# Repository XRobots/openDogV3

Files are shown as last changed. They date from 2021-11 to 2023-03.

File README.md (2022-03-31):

# openDogV3
CAD and Code for openDog V3: https://www.youtube.com/playlist?list=PLpwJoq86vov8uTgd8_WNgBHFpDYemO-OJ

I've included a Bill of Materials this time, BOM.ods, which is probably complete, I'll be adding to it if I remember anything else.

I used the AS5047 encoders in absolute position mode in this build. Check out the ODrive documentation for more info: https://docs.odriverobotics.com/v/latest/encoders.html You will have to configure the encoder parameters and then run the offset calibration as per the ODrive docmentation. Default offsets are set in the code in the variable declaration section which will need calibrating to move the joints to the default positons in mode 3 below.

ODrive vel_limit and vel_limit_tolerance are set to math.inf within the ODrive tool which stops the motors disarming under certain circumstanses. (You will have to do 'import math' first within the ODrive tool).

Menu options on the Dog/LCD are as follows:

0) nothing / default at power up
1) put motors into closed loop control
2) move legs outwards so they just clear the stand stirrups by 1-2 mm
3) move legs so both shoulder and knee joints are at 45' (the default positions shown in the CAD)
4) turn up motor position, velocity and integrator gains
5) inverse kinematics demo mode for 6 axis of translation and rotation (also makes the legs slightly straighterCancel changes)
6) walking mode (same leg position as 5)
10) put the feet back into position so they rest on the stand stirrups

The remote now has a 'reverse' switch which reverses four axis of the remote so the dog walks backwards. This happens on the remote rather than in the dog's kinematics. There is also a motor enable switch which must be on for the dog to work.

Foot mould CAD is included for silicone rubber feet. I used a 25A Shore hardness Platinum cure silicone with pigment. Note that the Carbon Fibre foot tube is glued into the lower leg and foot insert to stop it rotating.

The parts are all printed in PLA. The larger parts are around 15% infill with 3 perimeters at 0.3mm layer height. The smaller parts such as the Cycloidal drive internals are 4 perimeters and up to 30-40% infill.

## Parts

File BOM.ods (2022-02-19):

Part | desc | quantity | notes | Example item
General Parts
Motor | 9225 90 KV brishless motor | 12 | Either HobbyKing / Turnigy Multistar 9225 90 KV or EaglePower 8308 (stator) 9225 (can) 90 KV motors. | https://www.aliexpress.com/item/4000563826414.html
Belts | HTD 5M pitch 630mm length | 4 | Knee drive belts | https://www.beltingonline.com/htd-pitches-c-40_253/5mm-htd-timing-belts-p-4575.html
Carbon Fiber tube | 28mm OD, 1mm+ wall thickness | 4 | 4 x 1 metre lengths cut to size to match the CAD (cut-offs from the main parts are long enough for the legs) | https://www.ebay.co.uk/itm/333609712747
Electronics
ODrive BLDC motor drivers | ODrive 3.6 | 6 | 2 per axis | https://odriverobotics.com/shop/odrive-v36
Motor encoders | AMS AS5047P motor encoder | 12 | 1 per axis | https://www.digikey.co.uk/en/products/detail/AS5047P-TS_EK_AB/AS5047P-TS_EK_AB-ND/5452344
Microcontroller | Teensy 4.1 | 1 | For Dog | https://coolcomponents.co.uk/products/teensy-4-1-development-board
Microcontroller | Teensy LC | 1 | For Remote | https://coolcomponents.co.uk/products/teensy-lc-with-bootloader
Voltage Regulator | 5V / adjustable regulator | 1 | For Dog electronics - set to 5V to power Teensy etc | https://www.ebay.co.uk/itm/153278406120
IMU | MPU6050 | 1 | For Dog | https://coolcomponents.co.uk/products/mpu-6050-6-dof-accel-and-gyro-sensor-stemma-qt-qwiic
Radio | NRF24L01 | 2 | One in remote and one in Dog | https://www.amazon.co.uk/AZDelivery-NRF24L01-wireless-Arduino-ESP8266/dp/B075DBDS3J
Connectors | 25-Way D-range male | 1 |  | https://www.ebay.co.uk/itm/252433532104
Connectors | 25-Way D-range female | 1 |  | https://www.ebay.co.uk/itm/262493128741
Electronics power switch | latching push switch | 1 |  | https://www.ebay.co.uk/itm/282092882727
E-stop switch | latching push switch | 2 |  | https://www.amazon.co.uk/gp/product/B08927GP2J
Volt Meters | Pan Volt Meters | 2 |  | https://www.amazon.co.uk/gp/product/B07J2NQSFG
LCD | I2C backpack LCD | 1 |  | https://www.amazon.co.uk/Youmile-Interface-Adapter-Arduino-Raspberry-1602-Blue/dp/B08218RPX6
Encoder cable | 6-core foil-sheilded signail cable | 6 | metres, but make sure you have enough | https://www.cef.co.uk/catalogue/products/2592862-6-core-belden-equiv-9536-lsf-shielded-cable-sold-by-the-mtr
Joysticks | 3 axis Joystick | 2 | For remote | https://www.ebay.co.uk/itm/174872424256?epid=18034324627
toggle switches | on/off toggles | 5 | For remote | https://www.ebay.co.uk/itm/133684848765
Push switches | momentary switches | 4 | For remote | https://www.amazon.co.uk/gp/product/B089K8ZTC2
Batteries
Main Battery | 6S High-drain Lipo | 1 | Make sure it can source enough current, mineis 60C. Also requires suitable balance charger | https://hobbyking.com/en_us/zippy-compact-4000mah-6s-60c-lipo-pack.html
Electronics Battery | 2S small battery | 1 | Anything like 2S/3S will do - regulator above is used to get 5V anyway | https://www.amazon.co.uk/URGENEX-Battery-Batteries-1000mah-WLtoys/dp/B08Y8YN283
Breaings
Internal Cycloidal Drive bearings | 12mm OD x 4mm ID x 4mm thickness | 384 | I got these from Aliexpress for $70 for 400. | https://www.aliexpress.com/item/32814388857.html
Cam and cap Drive bearings | 32mm OD x 20mm ID x 7mm thickness | 36 | There are three per drive | https://www.aliexpress.com/item/896891895.html
Top/bottom Drive bearings | 85mm OD x 65mm ID x 10mm thickness | 24 | two per drive | https://www.aliexpress.com/item/4000110681895.html
Thin wall bearings | 37mm OD x 30mm ID x 4mm thickness | 8 | one per leg and two per end bracket. | https://simplybearings.co.uk/shop/p156409/61706ZZ-Budget-Metal-Shielded-Thin-Section-Deep-Groove-Ball-Bearing-30x37x4mm/product_info.html
Knee bearings | 22mm OD x 8mm ID x 7mm thickness | 8 | two per leg for the knee joints | https://simplybearings.co.uk/shop/p170659/608ZZ-Budget-Metal-Shielded-Deep-Groove-Ball-Bearing-8x22x7mm/product_info.html
Knee idler bearings | 19mm OD x 6mm ID, x 6mm thickness | 16 | four per leg for belt idler | https://simplybearings.co.uk/shop/p170642/626ZZ-Budget-Metal-Shielded-Deep-Groove-Ball-Bearing-6x19x6mm/product_info.html
4mm steel bar | 4mm x 31mm length | 132 | one for very bearing mount aroudn the outside of the cycloidal drives | https://www.ebay.co.uk/itm/193950943958
Nuts & Bolts
Motor mounts | M4 12 mm thread length countersunk | 48 | 4 per motor
Cycloidal Drive cam | M4 40mm thread length socket cap | 12 | 1 per drive
Cycloidal Drive cam | M4 Nylon insert locking nuts | 12 | 1 per drive
Cycloidal Drive output | M4 Nylon insert locking nuts | 60 | 5 per drive
Cycloidal Drive output | M4 washers | 60 | 5 per drive
Cycloidal Drive cam | M3 15mm thread length | 48 | 4 per drive
Cycloidal Drive output | M4 hex heads 80mm | 60 | 5 per drive, need cutting to length
Screws
Drive case screws | 2.9mm 18mm length countersunk pozidrive | 132 | 22 per drive, back and front
side-to-side axis mount screws | 2.9mm 18mm length countersunk pozidrive | 48 | 12 per drive for 4 drives
Leg screws | 2.9mm 18mm length countersunk pozidrive | 56 | 18 per leg
Nylon
Washers | 4mm ID Nylon washers | 384 | one top and bottom on each pin, 32 per drive | https://nyfast.com/nylon-washers/10080-26805-standard-flat-nylon-washers
Spacers | 4mm ID Nylon spacers, 5mm length | 192 | 16 per drive | https://nyfast.com/new-products/10497-30283-standard-metric-nylon-spacers

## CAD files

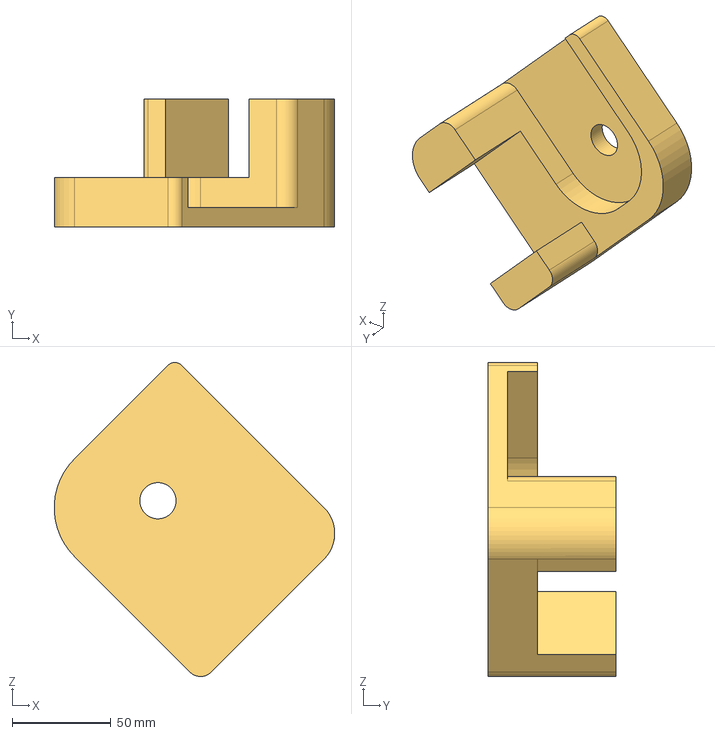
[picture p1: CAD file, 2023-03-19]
CAD/openDogV3_jig_knee.stp
142.3 x 65.0 x 159.4 mm

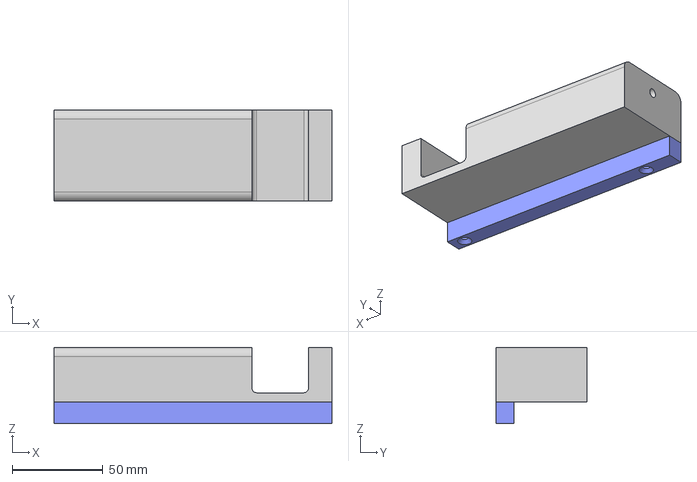
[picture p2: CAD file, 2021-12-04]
CAD/jig.stp
153.0 x 50.0 x 42.0 mm

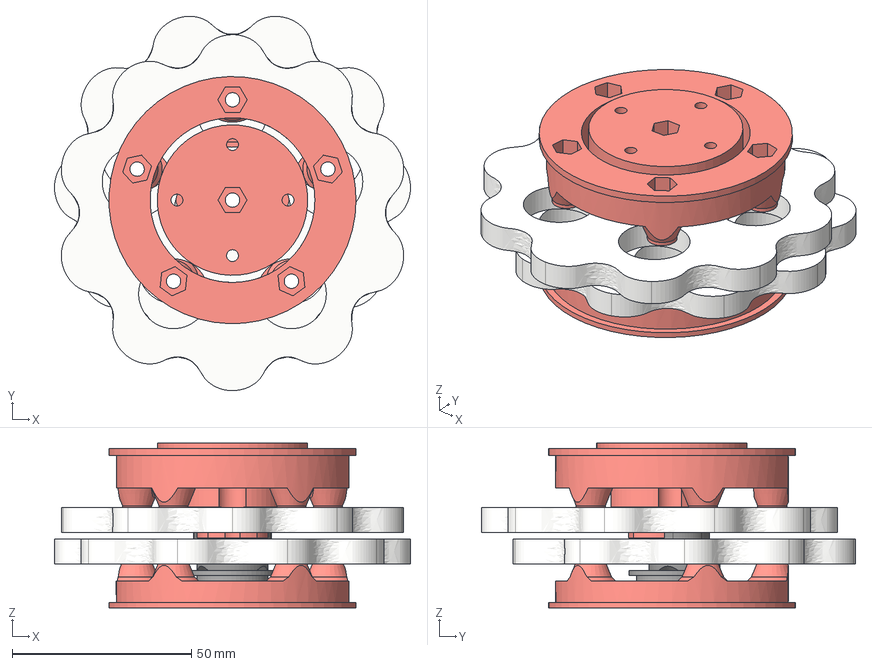
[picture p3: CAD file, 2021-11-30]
CAD/openDog V3_internals_toleranced.stp
99.4 x 104.5 x 46.0 mm

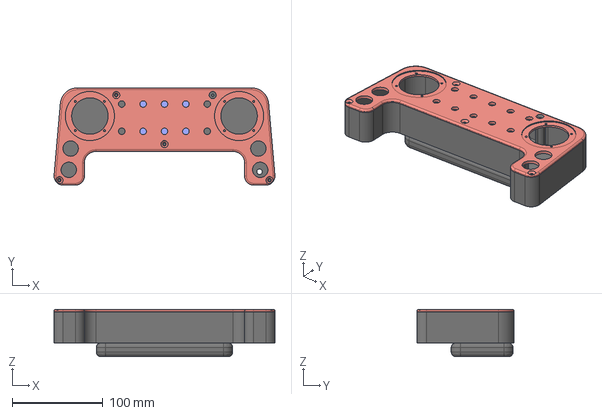
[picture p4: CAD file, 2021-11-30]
CAD/Remote.stp
242.9 x 107.0 x 52.0 mm

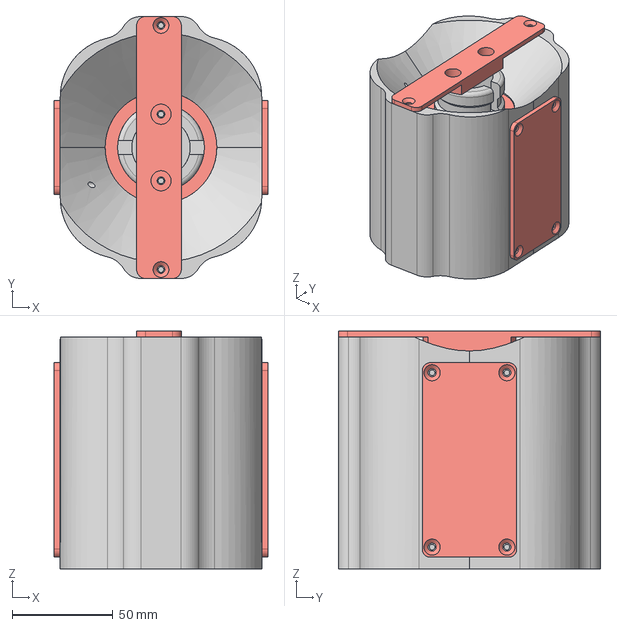
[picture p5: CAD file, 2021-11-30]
CAD/openDog V3_foot.stp
106.0 x 130.0 x 118.0 mm

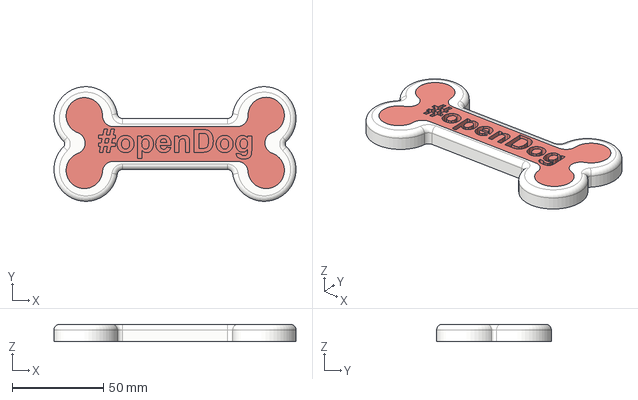
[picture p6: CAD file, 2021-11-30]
CAD/bone.stp
132.9 x 63.0 x 9.50 mm

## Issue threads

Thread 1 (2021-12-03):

BOM Edit - Steel Rod

twodawg, 2021-12-03:
Can you let us know how long (and how many) and the diameter size (4 mm?) you used as a steel rod to hold the bearings in each motor housing? I did not see it in the BOM.

I am super excited to upgrade my V2 Opendog to V3!

XRobots, 2021-12-04:
Thanks, I updated the BOM and also uploaded the jig I used to cut them. 31mm long, 4mm diameter.

ghent360, 2022-01-05:
Btw one can order 30mm long 4mm dowel pins. It would be great if those can be used. Alternatively the next standard size is 35mm.

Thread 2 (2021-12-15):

Account for Foot in Kinematics

Yay295, 2021-12-15:
Based on this diagram from your [kinematics video](https://www.youtube.com/watch?v=eKZIJwJBjEs), the end point of the leg is currently at the tip of the foot. However, as you stated in the video, the tip of the foot is not necessarily the point touching the ground. To account for this the end point of the leg should actually be at the center of the foot when doing the calculations. The point touching the ground would then be one foot's radius from this point.

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

XRobots, 2021-12-15:
Yes the legs are too short - in V2 I used the middle of the ball, so the CF tubes should just be a bit longer.  The centre positions will change as the foot rolls over though so there's still some error. Either way the whole thing is compliant so it's negligible.

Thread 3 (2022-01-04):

Encoders in BOM

ghent360, 2022-01-04:
Hi, are the encoders listed in the bom the ones you use in the video. By looking at the link the specified ones are just AMS magnetic encoder on a PCB with a magnet. The ones I see in your videos look quite different with a whole housing.

ghent360, 2022-01-04:
Also the magnetic encoders would need a magnet of some sort to be attached to the axis, do these come with the motor board?

XRobots, 2022-01-04:
I updated the BOM with links, it's this one, and it ships with the magnet: https://www.digikey.co.uk/en/products/detail/AS5047P-TS_EK_AB/AS5047P-TS_EK_AB-ND/5452344

ghent360, 2022-01-05:
Thank you. I saw you use the boards in one of your other videos.

Closed 2022-01-05.

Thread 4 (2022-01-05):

STL files and print instructions

ghent360, 2022-01-05:
Thank you for publishing the CAD files as open source.

Would it be possible to extract the STL files for the 3d printer parts and provide some guidance as how to best print those parts?
For example the part orientation, print settings like (number of perimeter walls, infill percentage, support material?)

For parts that need to be printed multiple times, I would recommend adding a suffix _xN (where N is the number of times the part needs to be printed). Also if you want to provide some guidance to the part color you can name parts should be printed in "alternate" color with a_ prefix.

(I would not take credit for this naming scheme, it is used by the Voron printer project and it works well there)

danielwdunn, 2022-06-08:
Hello, I'm looking for the same information/guidance. Did you happen to print this already or export the STLs from the step files?

XRobots, 2022-06-08:
It's designed to all be printed in PLA, but you could use tougher materials and skinny some of it down. I used 4 perimeters for everything at 0.3mm layer height with a 0.5mm nozzle. Infill was down to 10-15% for the big parts and 20-30% for the small parts like the cycloidal discs/small motor components etc.

ghent360, 2022-06-09:
First I want to say thank you to James for sharing this excellent project. It seems a lot of though went into it and I really appreciate the chance to be able to replicate your work.

I agree exporting the STLs seems like a tedious task. The trick is not to 3d print the models of the bearings, but one learns.

@XRobots for the internals of the transmission parts should one use the file called 'openDog V3_internals_toleranced' ?

danielwdunn, 2022-06-09:
Truly an incredible and impressive OpenSource project. I'm hoping to put together a full build guide for openDog v3 (if one doesn't exist yet). And I will include the information provided here and any I learn along the way.

XRobots, 2022-06-09:
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

That is another set of parts I toleranced for my printer.

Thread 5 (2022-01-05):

Add battery types to the BOM

ghent360, 2022-01-05:
I guess from your video the main battery is some 6S lipo type.

Can you also add the electronics and remote battery types?

XRobots, 2022-01-05:
I'll add the batteries to the BOM. Yes the main battery is 6S but it's quite high drain, so I have 60C battery(s).

The smaller one powering the electronics is 7.4v - I'll find a link for it, but anything over 6v will do.

Closed 2022-01-07.

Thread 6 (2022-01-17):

Please add the idler bearing to BOM

ghent360, 2022-01-17:
Your test leg video mentions 6mm ID bearings for the idlers, that are not in the BOM. Please add.

XRobots, 2022-01-17:
done, thanks

Closed 2022-01-17.

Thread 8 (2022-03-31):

Broken link

3laws, 2022-03-31:
Link [https://docs.odriverobotics.com/encoders](https://docs.odriverobotics.com/encoders)  is 404

XRobots, 2022-03-31:
ODrive updated their documentation - I've edited the link

Closed 2022-03-31.

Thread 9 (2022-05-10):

STP file disassembly is not working

MateKristof, 2022-05-10:
Could You tell me what is the CAD software do You use? When I open the STP file in Solid Edge or Inventor then the assembled parts in the assembly appears as only one big standart parts. I am not able to disassemble them. As You see in the shoulder connections:

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

**I would highly appreciate if You were kind and upload the native CAD software files**, like SolidWorks .sldprt / .sldasm or Solid Edge .par / .asm and so on.

XRobots, 2022-05-11:
It was done in Fision360, but it's a STEP file so it's just a bunch of solid objects. I know there are several people who are building it...  I've never used Inventor I'm afraid.

ghent360, 2022-06-09:
Some CAD software does have issues with the STEP file from fusion. I did use some STEP file analyzer (https://www.nist.gov/services-resources/software/step-file-analyzer-and-viewer) and it found no issues with the STEP file per se, so it has to be something in the import that chokes.

What I found works best is if you import the step file back in fusion 360 and then you can re-export only parts and that works a bit better.

Best of luck.

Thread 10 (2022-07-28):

Assemblies for Different CAD Programs

DrYogurt, 2022-07-28:
I'm having some difficulties importing the step files as assemblies (In FreeCAD SolidWorks and Fusion) parts load in as bodies and no import settings seem able to fix it. This is probably due to my inexperience with importing stps, but I would appreciate a zip of a Fusion or SolidWorks assembly.

Thanks

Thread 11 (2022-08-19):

ODrive 3.6 Voltage?

danielwdunn, 2022-08-19:
What voltage should be selected when ordering the ODrive 3.6?

Are there alternatives to this item? It's currently the most expensive piece of the entire project. Total cost is about $1500 USD for the six pieces of ODrive 3.6. Though, I did find another supplier on Aliexpress that may reduce the price to around $1000 or so.

XRobots, 2022-08-19:
I bought the 56V version because a 6S lipo will charge up to 25V+

I've not tried any alternatives. I haven't tried the ones on Aliexpress but they are likely to be clones of random hardware versions so the latest firmware may not work correctly.

danielwdunn, 2022-08-19:
Thank you! I ordered the Aliexpress 56v version and will test it. I'm working on an updated BOM for folks in the US/North America. I'll share it once complete.

dylanireland, 2022-11-02:
@danielwdunn Have you happened to receive and/or test the Aliexpress clone of the ODrive? Very interested to see your BOM when complete!

XRobots, 2022-11-03:
I've not tried them, but a lot of them look like the pins aren't in the same place, so they are clones of previous versions of hardware which means the pin mappings will be wrong and not everything will work as expexted.

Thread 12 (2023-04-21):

BOM: 5mm HTD® Timing Belts Width ?

bryn51, 2023-04-21:
Please specify the width of the timing belts needed.  Choices (standard) are 9 mm, 15 mm and 25 mm.  I'm guessing it might be 15 mm

ronzelver, 2023-04-21:
> Please specify the width of the timing belts needed.  Choices (standard) are 9 mm, 15 mm and 25 mm.  I'm guessing it might be 15 mm

15mm might just fit, but the ones I've used are 9mm wide and I think those are the ones originally referenced by James as well.

bryn51, 2023-04-21:
All good, thanks.

If not obvious, I am trying to cost out the project using the BOM.

Cheers

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

bryn51, 2023-04-24:
Thanks for your response.

Just by the by... looks like just buying the stuff needed is nightmareish. I discovered the chinese manufacturers of CF tubing do not even have testing facilities for their tubing, cant tell me how stiff is the tubing or what the breaking point(s) are.  Maybe I should be less persnickety.

f-e-l-i-x, 2023-05-31:
@ronzelver I saw your finished openDog on youtube, looks great! How much would I have to spend on building one of them?

ronzelver, 2023-05-31:
> @ronzelver I saw your finished openDog on youtube, looks great! How much would I have to spend on building one of them?

Total cost is around 2500~3000 EUR. The drives, controllers and bearings alone were already 1850 EUR.

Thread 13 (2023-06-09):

Suggestion: Checkout Dingo open source robot dog

lucasfolino, 2023-06-09:
Found this and thought you could use some of the techniques to further improve openDog.  Especially the linkage for the legs.  It seems to have better stability, control, and range of motion.  Also seems to have better response.  The Dingo isn't as long or string, but I think that these techniques could vastly improve the operation of open dog.  Also seems like they solved other issues as well.

https://www.youtube.com/watch?v=8KntOIgzUjY
https://github.com/Yerbert/DingoQuadruped
https://grabcad.com/library/dingo-robot-quadruped-2

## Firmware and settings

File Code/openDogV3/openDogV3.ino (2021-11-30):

//ODrive
#include <ODriveArduino.h>

// Radio
#include <SPI.h>
#include <nRF24L01.h>
#include <RF24.h>

//I2C LCD
#include <LiquidCrystal_I2C.h>
LiquidCrystal_I2C lcd(0x27, 16, 2); // set the LCD address to 0x27 for a 16 chars and 2 line display

// ramp lib
#include <Ramp.h>

RF24 radio(9, 10); // CE, CSN
const byte addresses[][6] = {"00001", "00002"};

// Printing with stream operator
template<class T> inline Print& operator <<(Print &obj,     T arg) {
  obj.print(arg);
  return obj;
}
template<>        inline Print& operator <<(Print &obj, float arg) {
  obj.print(arg, 4);
  return obj;
}


//ODrive Objects
ODriveArduino odrive1(Serial1);
ODriveArduino odrive2(Serial2);
ODriveArduino odrive3(Serial3);
ODriveArduino odrive4(Serial4);
ODriveArduino odrive5(Serial5);
ODriveArduino odrive6(Serial6);

//**************remote control****************
struct RECEIVE_DATA_STRUCTURE {
  //put your variable definitions here for the data you want to send
  //THIS MUST BE EXACTLY THE SAME ON THE OTHER ARDUINO
  int16_t menuDown;
  int16_t Select;
  int16_t menuUp;
  int16_t toggleBottom;
  int16_t toggleTop;
  int16_t toggle1;
  int16_t toggle2;
  int16_t mode;
  int16_t RLR;
  int16_t RFB;
  int16_t RT;
  int16_t LLR;
  int16_t LFB;
  int16_t LT;
};

RECEIVE_DATA_STRUCTURE mydata_remote;

int toggleTopOld;
int remoteState;
int remoteStateOld;

float RLR = 0;
float RFB = 0;
float RT = 340;
float LLR = 0;
float LFB = 0;
float LT = 0;

float RLRFiltered = 0;
float RFBFiltered = 0;
float RTFiltered = 340;
float LLRFiltered = 0;
float LFBFiltered = 0;
float LTFiltered = 0;
int filterFlag1 = 0;

unsigned long currentMillis;
long previousMillis = 0;    // set up timers
long interval = 10;        // time constant for timer
unsigned long count;

long previousInterpMillis = 0;    // set up timers
int interpFlag = 0;

unsigned long remoteMillis;

int stepFlag = 0;
long previousStepMillis = 0;
int stepStartFlag = 0;

int requested_state;
int mode;
int modeOld;
int modeFlag;
int menuFlag;
int modeConfirm;
int modeConfirmFlag = 0;
int runMode = 0;

float longLeg1;
float shortLeg1;
float legLength1;
float longLeg2;
float shortLeg2;
float legLength2;
float footOffset;

float fr_RFB;
float fl_RFB;
float bl_RFB;
float br_RFB;
float fr_RLR;
float fl_RLR;
float bl_RLR;
float br_RLR;;
float fr_LT;
float fl_LT;
float bl_LT;
float br_LT;

float fr_LLR;
float fl_LLR;
float br_LLR;
float bl_LLR;

float actPos1;
float actPos2;
float actPos3;
float actPos4;

int timer1;   // FB gait timer
int timer2;   // LR gait timer
int timer3;   // Yaw gait timer
float timerScale;   // resulting timer after calcs
float timerScale2;   // multiplier

// ODrive offsets from power up
// ratio is 10:1 so 1 'turn' is 36'.


float offSet20 = -0.3;      //ODrive 2, axis 0     // knee - right front
float offSet30 = 0.6;      //ODrive 3, axis 0     // knee - right rear
float offSet50 = 0.15;      //ODrive 5, axis 0     // knee - left front
float offSet60 = 0.05;      //ODrive 6, axis 0     // knee - left rear

float offSet21 = 0;      //ODrive 2, axis 1     // shoulder - right front
float offSet31 = 0.35;      //ODrive 3, axis 1     // shoulder - right rear
float offSet51 = 0.55;      //ODrive 5, axis 0     // shoulder - left front
float offSet61 =  0.05;      //ODrive 6, axis 1     // shoulder - left rear

float offSet10 = 0.27;      //ODrive 1, axis 0     // hips - right front
float offSet11 = 0.1;      //ODrive 1, axis 1     // hips - right back
float offSet40 = 0.07;      //ODrive 4, axis 0     // hips - left front
float offSet41 = 0.35;      //ODrive 4, axis 1     // hips - left back


// ** test varibles

      int tester;
      int tester2;
      //long previousStepMillis = 0;    // set up timers
      //int stepFlag = 0;
      float z;
      float x;


//***********************************
//***********************************
class Interpolation {
  public:
    rampInt myRamp;
    int interpolationFlag = 0;
    int savedValue;

    int go(int input, int duration) {

      if (input != savedValue) {   // check for new data
        interpolationFlag = 0;
      }
      savedValue = input;          // bookmark the old value

      if (interpolationFlag == 0) {                                        // only do it once until the flag is reset
        myRamp.go(input, duration, LINEAR, ONCEFORWARD);              // start interpolation (value to go to, duration)
        interpolationFlag = 1;
      }

      int output = myRamp.update();
      return output;
    }
};    // end of class

Interpolation interpFRX;        // interpolation objects
Interpolation interpFRY;
Interpolation interpFRZ;
Interpolation interpFRT;

Interpolation interpFLX;        // interpolation objects
Interpolation interpFLY;
Interpolation interpFLZ;
Interpolation interpFLT;

Interpolation interpBRX;        // interpolation objects
Interpolation interpBRY;
Interpolation interpBRZ;
Interpolation interpBRT;

Interpolation interpBLX;        // interpolation objects
Interpolation interpBLY;
Interpolation interpBLZ;
Interpolation interpBLT;

//***********************************
//***********************************

// ****************** SETUP ******************************

void setup() {


  // initialize serial communication
  Serial.begin(115200);

  Serial1.begin(115200);
  Serial2.begin(115200);
  Serial3.begin(115200);
  Serial4.begin(115200);
  Serial5.begin(115200);
  Serial6.begin(115200);


  radio.begin();
  radio.openWritingPipe(addresses[0]); // 00002
  radio.openReadingPipe(1, addresses[1]); // 00001
  radio.setPALevel(RF24_PA_MIN);

  radio.startListening();

  //LCD
  lcd.init();
  lcd.backlight();
  lcd.setCursor(0, 0);
  lcd.print("openDog V3");
  lcd.setCursor(0, 1);
  lcd.print("S:0  C:0");

}   // end of setup

// ********************* MAIN LOOP *******************************

void loop() {

  currentMillis = millis();
  if (currentMillis - previousMillis >= 10) {  // start timed event

    previousMillis = currentMillis;


    // check for radio data
    if (radio.available()) {
      radio.read(&mydata_remote, sizeof(RECEIVE_DATA_STRUCTURE));
      remoteMillis = currentMillis;
    }

    // is the remote disconnected for too long ?
    if (currentMillis - remoteMillis > 500) {
      remoteState = 0;
    }
    else {
      remoteState = 1;
    }    

    // threshold remote data
    // some are reversed based on stick wiring in remote
    RFB = (thresholdStick(mydata_remote.RFB)) * -1;
    RLR = (thresholdStick(mydata_remote.RLR));
    RT = thresholdStick(mydata_remote.RT);
    LFB = (thresholdStick(mydata_remote.LFB)) * -1;
    LLR = thresholdStick(mydata_remote.LLR);
    LT = thresholdStick(mydata_remote.LT);

    
    // stop the dog if the remote becomes disconnected
    if (remoteState == 0) {     
      RFB = 0;
      RLR = 0;
      RT = 0;
      LFB = 0;
      LLR = 0;
      LT = 0;
    }


    // mode select

    if (mydata_remote.menuUp == 1 && menuFlag == 0) {
      menuFlag = 1;
      mode = mode + 1;
      mode = constrain(mode, 0, 10);
    }
    else if (mydata_remote.menuDown == 1 && menuFlag == 0) {
      menuFlag = 1;
      mode = mode - 1;
      mode = constrain(mode, 0, 10);
    }
    else if (mydata_remote.menuDown == 0 && mydata_remote.menuUp == 0) {
      menuFlag = 0;
    }

    if (mode != modeOld) {            // only update the LCD if the data has changed
      lcd.setCursor(0, 1);
      lcd.print("    ");
      lcd.setCursor(0, 1);
      lcd.print("S:");
      lcd.print(mode);
    }
    modeOld = mode;       // bookmark previous data so we can see if it's changed

    if (mydata_remote.Select == 1) {
      modeConfirm = mode;             // make the actual mode be the potential mode when the select button is pressed
      lcd.setCursor(5, 1);            // display current mode on LCD
      lcd.print("    ");
      lcd.setCursor(5, 1);
      lcd.print("C:");
      lcd.print(modeConfirm);
    }

    // display remote connection state
    if (remoteState != remoteStateOld) {
      if (remoteState == 0) {
        lcd.setCursor(13, 0);
        lcd.print("N");
      }
      else if (remoteState == 1) {
        lcd.setCursor(13, 0);
        lcd.print("C");
      }
    }
    remoteStateOld = remoteState;

    // display motor enable state

    if (mydata_remote.toggleTop != toggleTopOld) {
      if (mydata_remote.toggleTop == 1) {
        lcd.setCursor(15, 0);
        lcd.print("E");
      }
      else if (mydata_remote.toggleTop == 0) {
        lcd.setCursor(15, 0);
        lcd.print("D");
      }
    }
    toggleTopOld = mydata_remote.toggleTop;

    // ****** MAIN MENU ******* 

    if (mydata_remote.Select == 0) {                            // make sure the button is released before it can be pressed again
              modeConfirmFlag = 0;
    }

    if (modeConfirm == 1 && modeConfirmFlag == 0 && mydata_remote.Select == 1) {             // init ODrives with low gains
      Serial.println("Init Odrives mode 1");
      OdriveInit1();
      modeConfirmFlag = 1;
    }

    else if (modeConfirm == 2 && modeConfirmFlag == 0 && mydata_remote.Select == 1) {       // default to 45' shoulder and knees
      Serial.println("Knees mode 2");
      applyOffsets1();
      modeConfirmFlag = 1;
    }

    else if (modeConfirm == 3 && modeConfirmFlag == 0 && mydata_remote.Select == 1) {       // default to hip position
      Serial.println("Shoulders mode 3");
      applyOffsets2();
      modeConfirmFlag = 1;
    }

    else if (modeConfirm == 4 && modeConfirmFlag == 0 && mydata_remote.Select == 1) {       // turn up gains
      Serial.println("Modify Gains mode 4");
      modifyGains();
      modeConfirmFlag = 1;
    }

    else if (modeConfirm == 5 && modeConfirmFlag == 0 && mydata_remote.Select == 1) {       // turn up gains
      Serial.println("Kinematics mode 5");
      interpFlag = 0;
      previousInterpMillis = currentMillis;
      runMode = 1;
      modeConfirmFlag = 1;
    }

    else if (modeConfirm == 6 && modeConfirmFlag == 0 && mydata_remote.Select == 1) {       // turn up gains
      Serial.println("Walking Mode 6");
      interpFlag = 0;
      previousInterpMillis = currentMillis;
      runMode = 2;
      modeConfirmFlag = 1;
    }

    else if (modeConfirm == 10 && modeConfirmFlag == 0 && mydata_remote.Select == 1) {       // turn up gains
      Serial.println("Going Home Mode 10");
      interpFlag = 0;
      previousInterpMillis = currentMillis;
      runMode = 10;
      modeConfirmFlag = 1;
    }

    else if (modeConfirm == 9 && modeConfirmFlag == 0 && mydata_remote.Select == 1) {       // turn up gains
      Serial.println("Interp Test");
      interpFlag = 0;
      previousInterpMillis = currentMillis;
      runMode = 9;
      modeConfirmFlag = 1;
    }
    
    // **** END OF MAIN MENU **** 

    if (runMode == 9) {     // iterpolation testing

      if (stepFlag == 0 && currentMillis - previousStepMillis > 1000) {
          tester = 0;
          tester2 = 300.5;
          stepFlag = 1;
          previousStepMillis = currentMillis;
          }

      else if (stepFlag == 1 && currentMillis - previousStepMillis > 1000) {
          tester = 100.6;
          tester2 = 0;
          stepFlag = 0;
          previousStepMillis = currentMillis;
          }

        z = interpFRZ.go(tester,500);
        x = interpFRY.go(tester2,500);
            
        Serial.print(stepFlag);
        Serial.print(" , ");
        Serial.print(tester);
        Serial.print(" , ");
        Serial.print(z);
        Serial.print(" , ");
        Serial.println(x);      
    }

    if (runMode == 10) {         // put the legs back on the stand

        int offset1 = 70;

        kinematics (1, -offset1, 0, 300, 0, 0, 0, 0, 0);   // front right
        kinematics (2, -offset1, 0, 300, 0, 0, 0, 0, 0);   // front left
        kinematics (3, offset1, 0, 300, 0, 0, 0, 0, 0);   // back left
        kinematics (4, offset1, 0, 300, 0, 0, 0, 0, 0);   // back right
    }

    else if (runMode == 1) {
      
    // ** inverse kinematics demo ** 

        // scale sticks to mm
        RFB = map(RFB,-462,462,-100,100);
        RLR = map(RLR,-462,462,-100,100);        
        RT = map(RT,-462,462,240,440);
        RT = constrain(RT,240,380);      
        LFB = map(LFB,-462,462,-15,15);        
        LLR = map(LLR,-462,462,-15,15);        
        LT = map(LT,-462,462,-20,20);      

        // filter sticks
        RFBFiltered = filter(RFB, RFBFiltered, 40);
        RLRFiltered = filter(RLR, RLRFiltered, 40);
        RTFiltered = filter(RT, RTFiltered, 40);
        LFBFiltered = filter(LFB, LFBFiltered, 40);
        LLRFiltered = filter(LLR, LLRFiltered, 40);
        LTFiltered = filter(LT, LTFiltered, 40);
                  
        kinematics (1, RFBFiltered, RLRFiltered, RTFiltered, LLRFiltered, LFBFiltered, LTFiltered, 0, 0);   // front right
        kinematics (2, RFBFiltered, RLRFiltered, RTFiltered, LLRFiltered, LFBFiltered, LTFiltered, 0, 0);   // front left
        kinematics (3, RFBFiltered, RLRFiltered, RTFiltered, LLRFiltered, LFBFiltered, LTFiltered, 0, 0);   // back left
        kinematics (4, RFBFiltered, RLRFiltered, RTFiltered, LLRFiltered, LFBFiltered, LTFiltered, 0, 0);   // back right
      
 }

   else if (runMode == 2) {
      // simple walking
      
      RFB = map(RFB,-462,462,-50,50);  // mm
      RLR = map(RLR,-462,462,-25,25);  // mm
      LT = map(LT,-462,462,-25,25);      // degrees 

      RFBFiltered = filter(RFB, RFBFiltered, 15);
      RLRFiltered = filter(RLR, RLRFiltered, 15);
      LTFiltered = filter(LT, LTFiltered, 15);

      longLeg1 = 340;
      shortLeg1 = 250;
      longLeg2 = 340;
      shortLeg2 = 250;

      footOffset = 0;
      timer1 = 75;   // FB gait timer
      //timer2 = 75;   // LR gait timer
      //timer3 = 75;   // LR gait timer

      if (RFBFiltered > -0.1 && RFBFiltered < 0.1 && RLRFiltered > -0.1 && RLRFiltered < 0.1  && LTFiltered > -0.1 && LTFiltered < 0.1 ) {    // controls are centred or near enough

      
      // position legs a default standing positionS
          legLength1 = longLeg1;
          legLength2 = longLeg2;
          fr_RFB = 0;
          fl_RFB = 0;
          bl_RFB = 0;
          br_RFB = 0;
          fr_RLR = footOffset;
          fl_RLR = -footOffset;
          bl_RLR = -footOffset;
          br_RLR = footOffset;
          fr_LT = 0;
          fl_LT = 0;
          bl_LT = 0;
          br_LT = 0;        
      }
      
      //walking
      else {


          //Serial.println(timerScale);
        
          if (stepFlag == 0 && currentMillis - previousStepMillis > timerScale) {
              legLength1  = shortLeg1;
              legLength2 = longLeg2; 
              fr_RFB = 0-RFBFiltered;
              fl_RFB = RFBFiltered;
              bl_RFB = 0-RFBFiltered;
              br_RFB = RFBFiltered;
              fr_RLR = (footOffset -RLRFiltered) + LT;
              fl_RLR = (-footOffset +RLRFiltered) - LT;
              bl_RLR = (-footOffset - RLRFiltered) - LT;
              br_RLR = (footOffset + RLRFiltered) + LT;
              //fr_RLR = LT;
              //fl_RLR = 0-LT;
              //bl_RLR = 0-LT;
              //br_RLR = LT;
              stepFlag = 1;              
              previousStepMillis = currentMillis;
          }

          else if (stepFlag == 1 && currentMillis - previousStepMillis > timerScale) {
              legLength1 = longLeg1;
              legLength2 = longLeg2;
              fr_RFB = 0-RFBFiltered;
              fl_RFB = RFBFiltered;
              bl_RFB = 0-RFBFiltered;
              br_RFB = RFBFiltered;
              fr_RLR = (footOffset -RLRFiltered) + LT;
              fl_RLR = (-footOffset +RLRFiltered) - LT;
              bl_RLR = (-footOffset -RLRFiltered) - LT;
              br_RLR = (footOffset +RLRFiltered) + LT;
              //fr_RLR = LT;
              //fl_RLR = 0-LT;
              //bl_RLR = 0-LT;
              //br_RLR = LT;                        

              stepFlag = 2;              
              previousStepMillis = currentMillis;
          }

          else if (stepFlag == 2 && currentMillis - previousStepMillis > timerScale) {
              legLength1 = longLeg1;
              legLength2 = shortLeg2;
              fr_RFB = RFBFiltered;
              fl_RFB = 0-RFBFiltered;
              bl_RFB = RFBFiltered;
              br_RFB = 0-RFBFiltered;
              fr_RLR = (footOffset +RLRFiltered) - LT;
              fl_RLR = (-footOffset -RLRFiltered) + LT;
              bl_RLR = (-footOffset +RLRFiltered) + LT;
              br_RLR = (footOffset -RLRFiltered) - LT;
              //fr_RLR = 0-LT;
              //fl_RLR = LT;
              //bl_RLR = LT;
              // br_RLR = 0-LT; 
              stepFlag = 3;              
              previousStepMillis = currentMillis;
          }

          else if (stepFlag == 3 && currentMillis - previousStepMillis > timerScale) {
              legLength1 = longLeg1;
              legLength2 = longLeg2;
              fr_RFB = RFBFiltered;
              fl_RFB = 0-RFBFiltered;
              bl_RFB = RFBFiltered;
              br_RFB = 0-RFBFiltered;
              fr_RLR = (footOffset +RLRFiltered) - LT;
              fl_RLR = (-footOffset -RLRFiltered) + LT;
              bl_RLR = (-footOffset +RLRFiltered) + LT;
              br_RLR = (footOffset -RLRFiltered) - LT;
              //fr_RLR = 0-LT;
              //fl_RLR = LT;
              //bl_RLR = LT;
              //br_RLR = 0-LT; 
              stepFlag = 0;              
              previousStepMillis = currentMillis;
          }

           
          float stepLength;
          float stepWidth;
          float stepAngle;
          float stepHyp;

          // timer calcs

          stepLength = abs(fr_RFB);
          stepWidth = abs(fr_RLR);

          if (stepLength == 0.0) {
            stepLength = 0.01;   // avoid divide by zero
          }

          stepAngle = atan(stepLength/stepWidth);  // radians       // work out actual distance of step
          stepHyp = abs(stepLength/sin(stepAngle));    // mm

          timerScale =  timer1 + (stepHyp/3.5);         
          
      }
   
      kinematics (1, fr_RFB, fr_RLR, legLength1, 0, 0, 0, 1, (timerScale*0.8));   // front right
      kinematics (2, fl_RFB, fl_RLR, legLength2, 0, 0, 0, 1, (timerScale*0.8));   // front left
      kinematics (3, bl_RFB, bl_RLR, legLength1, 0, 0, 0, 1, (timerScale*0.8));   // back left
      kinematics (4, br_RFB, br_RLR, legLength2, 0, 0, 0, 1, (timerScale*0.8));   // back right             
   }



  }     // end of timed loop

}       // end  of main loop

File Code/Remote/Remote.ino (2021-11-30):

#include <SPI.h>
#include <nRF24L01.h>
#include <RF24.h>

#include <Wire.h>  // Comes with Arduino IDE
#include <LiquidCrystal_I2C.h>

// Set the pins on the I2C chip used for LCD connections (Some LCD use Address 0x27 and others use 0x3F):
LiquidCrystal_I2C lcd(0x27,20,4);  // set the LCD address to 0x27 for a 16 chars and 2 line display

unsigned long previousMillis = 0;
const long interval = 20;

int but1;
int but2;
int but3;
int but4;

int sw1;
int sw2;
int sw3;
int sw4;
int sw5;

int axis1;
int axis2;
int axis3;
int axis4;
int axis5;
int axis6;

String count;

struct SEND_DATA_STRUCTURE{
//struct __attribute__((__packed__)) SEND_DATA_STRUCTURE{
  //put your variable definitions here for the data you want to send
  //THIS MUST BE EXACTLY THE SAME ON THE OTHER ARDUINO

    int16_t menuDown;  
    int16_t Select;    
    int16_t menuUp;  
    int16_t toggleBottom;  
    int16_t toggleTop; 
    int16_t toggle1;
    int16_t toggle2;
    int16_t mode;  
    int16_t RLR;
    int16_t RFB;
    int16_t RT;
    int16_t LLR;
    int16_t LFB;
    int16_t LT;

};

struct RECEIVE_DATA_STRUCTURE_REMOTE{
  //put your variable definitions here for the data you want to receive
  //THIS MUST BE EXACTLY THE SAME ON THE OTHER ARDUINO
  int16_t mode;
  int16_t count;
};

int remoteFlag = 0;

SEND_DATA_STRUCTURE mydata_send;
RECEIVE_DATA_STRUCTURE_REMOTE mydata_remote;

RF24 radio(14, 10); // CE, CSN
const byte addresses[][6] = {"00001", "00002"};


void setup() {  

  lcd.init();  // initialize the lcd 
  lcd.backlight();

  pinMode(0, INPUT_PULLUP);
  pinMode(1, INPUT_PULLUP);
  pinMode(2, INPUT_PULLUP);
  pinMode(3, INPUT_PULLUP);
  pinMode(4, INPUT_PULLUP);  
  pinMode(5, INPUT_PULLUP); 
  pinMode(6, INPUT_PULLUP); 
  pinMode(7, INPUT_PULLUP);
  pinMode(8, INPUT_PULLUP);
  
  pinMode(A1, INPUT);
  pinMode(A2, INPUT);
  pinMode(A4, INPUT);
  pinMode(A5, INPUT);
  pinMode(A6, INPUT);
  pinMode(A7, INPUT);
  
  radio.begin();
  radio.openWritingPipe(addresses[1]); // 00001
  radio.openReadingPipe(1, addresses[0]); // 00002
  radio.setPALevel(RF24_PA_MIN);

  radio.stopListening();

  lcd.begin(20,4);   // Initialize the lcd for 20 chars 4 lines, turn on backlight

  lcd.setCursor(0,0);
  lcd.print("Everything Remote   ");
  lcd.setCursor(0,1);
  lcd.print("XRobots.co.uk       ");

  Serial.begin(115200);
 
    
}

void loop() {

     unsigned long currentMillis = millis();
         if (remoteFlag == 0 && currentMillis - previousMillis >= 10) { 

              previousMillis = currentMillis;  

              but1 =  digitalRead(2);
              but2 =  digitalRead(3);
              but3 =  digitalRead(0);
              but4 =  digitalRead(1);

              sw1 = digitalRead(4);
              sw2 = digitalRead(5);
              sw3 = digitalRead(6);
              sw4 = digitalRead(8);
              sw5 = digitalRead(7);

                           
              if (but1 == 0) {
                mydata_send.menuDown = 1;
              }
              else {
                mydata_send.menuDown = 0;
              }

              if (but4 == 0) {
                mydata_send.Select = 1;
              }
              else {
                mydata_send.Select = 0;
              }
                            
              if (but2 == 0) {
                mydata_send.menuUp = 1;
              }
              else {
                mydata_send.menuUp = 0;
              }

              
              
              if (sw2 == 0) {
                mydata_send.toggleBottom = 1;
              }
              else {
                mydata_send.toggleBottom = 0;
              }
              
              if (sw1 == 0) {
                mydata_send.toggleTop = 1;
              }
              else {
                mydata_send.toggleTop = 0;
              }

              //******************

              if (sw3 == 0) {
                mydata_send.toggle1 = 1;
              }
              else {
                mydata_send.toggle1 = 0;
              }
              
              if (but3 == 0) {
                mydata_send.toggle2 = 1;
              }
              else {
                mydata_send.toggle2 = 0;
              } 
                       
              axis1 = analogRead(A5);
              axis2 = analogRead(A4);
              axis3 = analogRead(A6);
              axis4 = analogRead(A3);
              axis5 = analogRead(A2);
              axis6 = analogRead(A1);            

              axis2 = map(axis2,0,1023,1023,0);   // reverse some axis due to physical wiring
              axis4 = map(axis4,0,1023,1023,0);   // reverse some axis due to physical wiring

              // reverse walking & reverse all controls (twist is unaffected because CW and CCW and still the same no matter which way around it is)
              
              if (sw5 == 0) {
                axis1 = map(axis1,0,1023,1023,0);   // reverse axis
                axis2 = map(axis2,0,1023,1023,0);   // reverse axis
                axis4 = map(axis4,0,1023,1023,0);   // reverse axis
                axis5 = map(axis5,0,1023,1023,0);   // reverse axis
              }
              
              axis6 = map(axis6,0,1023,1023,0);   // reverse some axis due to physical wiring            
             
              mydata_send.RFB = axis1;
              mydata_send.RLR = axis2;
              mydata_send.RT = axis3;
              mydata_send.LFB = axis4;
              mydata_send.LLR = axis5;
              mydata_send.LT = axis6;              

              radio.write(&mydata_send, sizeof(SEND_DATA_STRUCTURE));               
              
         }        
        


      



  }  // end of main loop

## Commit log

2021-12-04 added jig CAD for cutting 4mm steel bars
    [jig.stp]
2021-12-04 added CAD for Jig, for cutting 4mm steel bars
2021-12-04 updated BOM to add 4mm steel bars
    [BOM.ods]
2021-12-20 Added links to example items
    [BOM.ods]
2022-01-05 updated BOM with batteries and regulator
    [BOM.ods]
2022-01-17 added leg belt idler bearings
    [BOM.ods]
2022-02-05 updated knee idler bearing quantity
    [BOM.ods]
2022-02-19 updated with remote switches and joysticks
    [BOM.ods]
2022-03-20 added code that uses the IMU
2022-03-20 CAD with longer lower leg and stirrup
2023-03-19 added knee jig
    [openDogV3_jig_knee.stp]
